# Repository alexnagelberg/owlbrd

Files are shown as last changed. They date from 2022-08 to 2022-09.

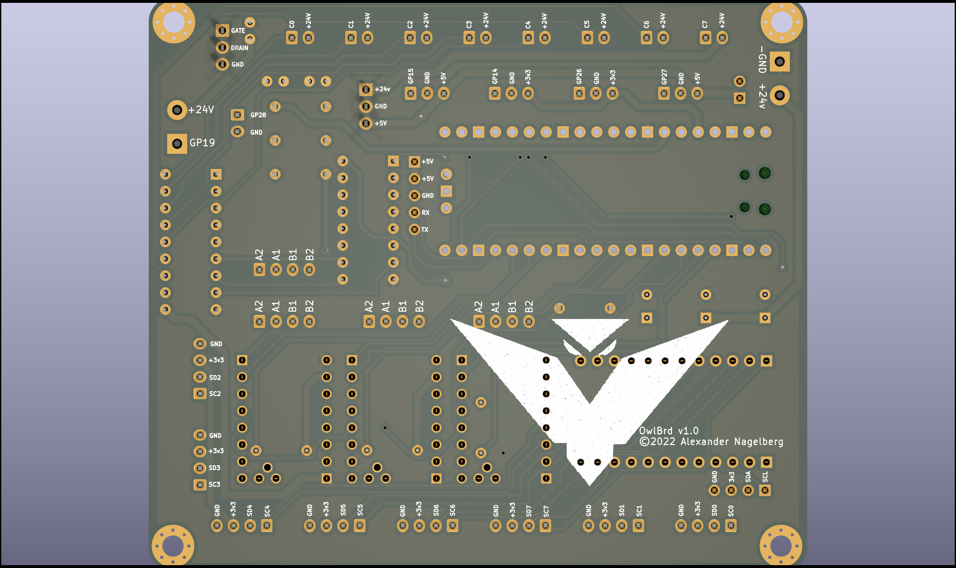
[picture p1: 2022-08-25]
images/back.png

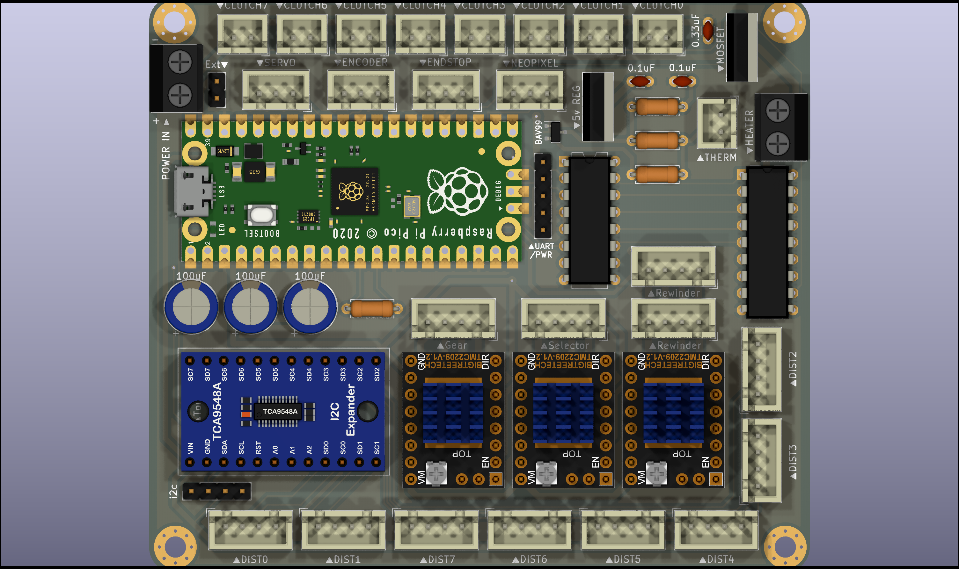
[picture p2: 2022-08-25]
images/board.png

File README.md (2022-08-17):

# OwlBrd
This board was made to supersede EasyBrd but it has a lot more to it so for cost or complexity, you can pick and choose what you want. The only section needed to drive 8 spools is the core section, ideally with distance sensors as well. Most of these parts can be found [in the US] on Amazon/Digikey and should be widely available and low cost and swappable with different manufacturers, the one exception being the optional TCA9548A breakout which only works with Adafruit's (maybe in future I'll add another row of pins to allow the hiletgo variants, but some workarounds can be done).

All the boards can be soldered either directly down or put down a set of headers so the boards can be removed/replaced. I would maybe take care with the TMC drivers as there's a resistor under each, but you could also solder the resistors on the bottom side if there's concerns of heat/proximity without a header -- probably shouldn't be an issue at all.

## BOM (split by functionality)

### Misc (listed again throughout sections)
 - Dupont male/female headers ([Amazon Affiliate](https://amzn.to/3ps0VLI))
 - Resistors - 1k, 10k, 2.37k, 4.7k used throughout (kit: [Amazon affiliate](https://amzn.to/3c7XxCF))
 - Ceramic capacitors: 0.33uF, 0.1uF used in ERCF/heater (kit: [Amazon affiliate](https://amzn.to/3wbLxqx))
 - Electrolytic capacitors: 100uF 25v used in ERCF/rewinder (kit: [Amazon affiliate](https://amzn.to/3Qs2sNM))
 - JST-XH connectors: 2-pin, 3-pin, 4-pin (kit: [Amazon affiliate](https://amzn.to/3AnAbBp))
 - Screw terminals for power/heater ([Amazon affiliate](https://amzn.to/3T8kE0O))

### Core (Rewind Stepper + Clutches)
- Raspberry Pi Pico ([[Digikey](https://www.digikey.com/en/products/detail/raspberry-pi/SC0915/13624793)] headers are optional)
- BTT TMC2209 x1 ([[Amazon affiliate](https://amzn.to/3prqGvD)] headers encouraged, note that UART is currently wired to the 4th pin and some like FYSETC use the 5th pin. You might be able to resolve this with a jumper on the pins on top?)
- 74HC238 DIP ([Amazon affiliate](https://amzn.to/3PAAPkm)) for clutch (addresses 8 pins using 3 GPIO)
- ULN2803A DIP ([Amazon affiliate](https://amzn.to/3QPcatl)) for clutch (drives 8 clutches using one IC)
- Screw terminal for power
- Resistors: 10k (x1), 1k (x1)
- JST-XH 2 pin female (x8) for clutches
- JST-XH 4 pin female (x2) for rewinder steppers
- Electrolytic capacitor: 100uF 25v

### Distance Sensors
- Adafruit TCA9548A ([Amazon affiliate](https://amzn.to/3wdmtQd) or [adafruit](https://www.adafruit.com/product/2717)) breakout (headers optional, cheaper generics available but one side is slightly wider by like 2.5mm -- might be able to rig something to fit it or could use wires)
- JST-XH 4 pin female (x8) for each sensor

### ERCF
- BTT TMC2209 x2 ([[Amazon affiliate](https://amzn.to/3prqGvD)] headers encouraged, note that UART is currently wired to the 4th pin and some like FYSETC use the 5th pin. You might be able to resolve this with a jumper on the pins on top?)
- L7805CV ([Amazon affiliate](https://amzn.to/3zYoTTM)) 5v linear regulator (probably plenty of substitutions for this but should be readily available -- any 5v regulator with same pinout should work) for supplying 5v power on board
- Resistors: 10k (x2)
- Ceramic capacitors: 0.33uF x1, 0.1uF x1
- Electrolytic capacitors: 100uF 25v (x2)
- JST-XH 3 pin female (x4) for servo, encoder, endstop, and optional neopixel/misc
- JST-XH 4 pin female (x2) for selector/gear steppers

### Heater
- IRLB8721PBF ([Amazon affiliate](https://amzn.to/3A3fAC1)) MOSFET (probably lots of substitutable options but should be readily available)
- BAV99 SMD ([[Amazon affiliate](https://amzn.to/3Pub5Gj)] only surface mount component -- shouldn't be too difficult to solder or need anything special, needed for thermistor)
- Screw terminal (or connector of your choice) for heater
- Resistors: 2.37k (x2), 4.7k (x1)
- Ceramic capacitor: 0.1uF
- JST-XH 2 pin female (for thermistor)

### UART
There's a breakout for UART with power for pi. If you use UART, and don't connect pico to USB, you'll want to put a header and jumper on J29 Ext Power so that it powers the pico from the 5v regulator. Install the 0.33uF and 0.1uF capacitors and L7805CV from ERCF section to get 5v power if needed.

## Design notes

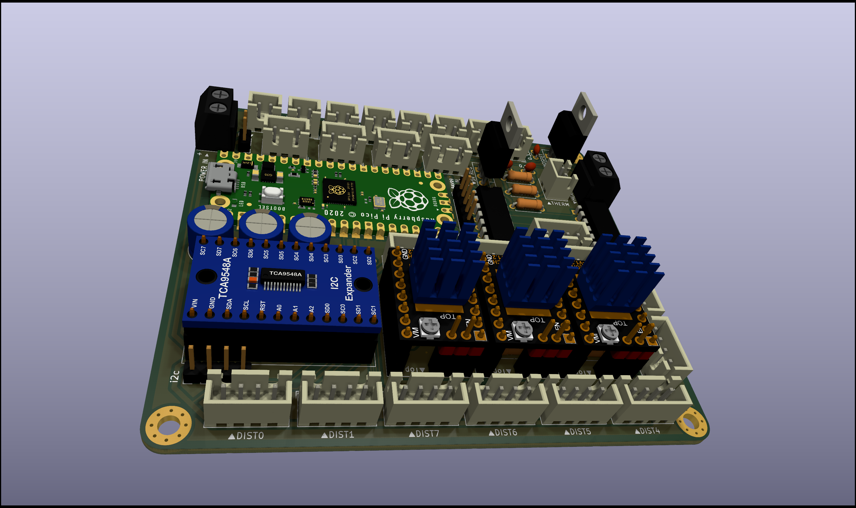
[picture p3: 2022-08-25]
images/board2.png

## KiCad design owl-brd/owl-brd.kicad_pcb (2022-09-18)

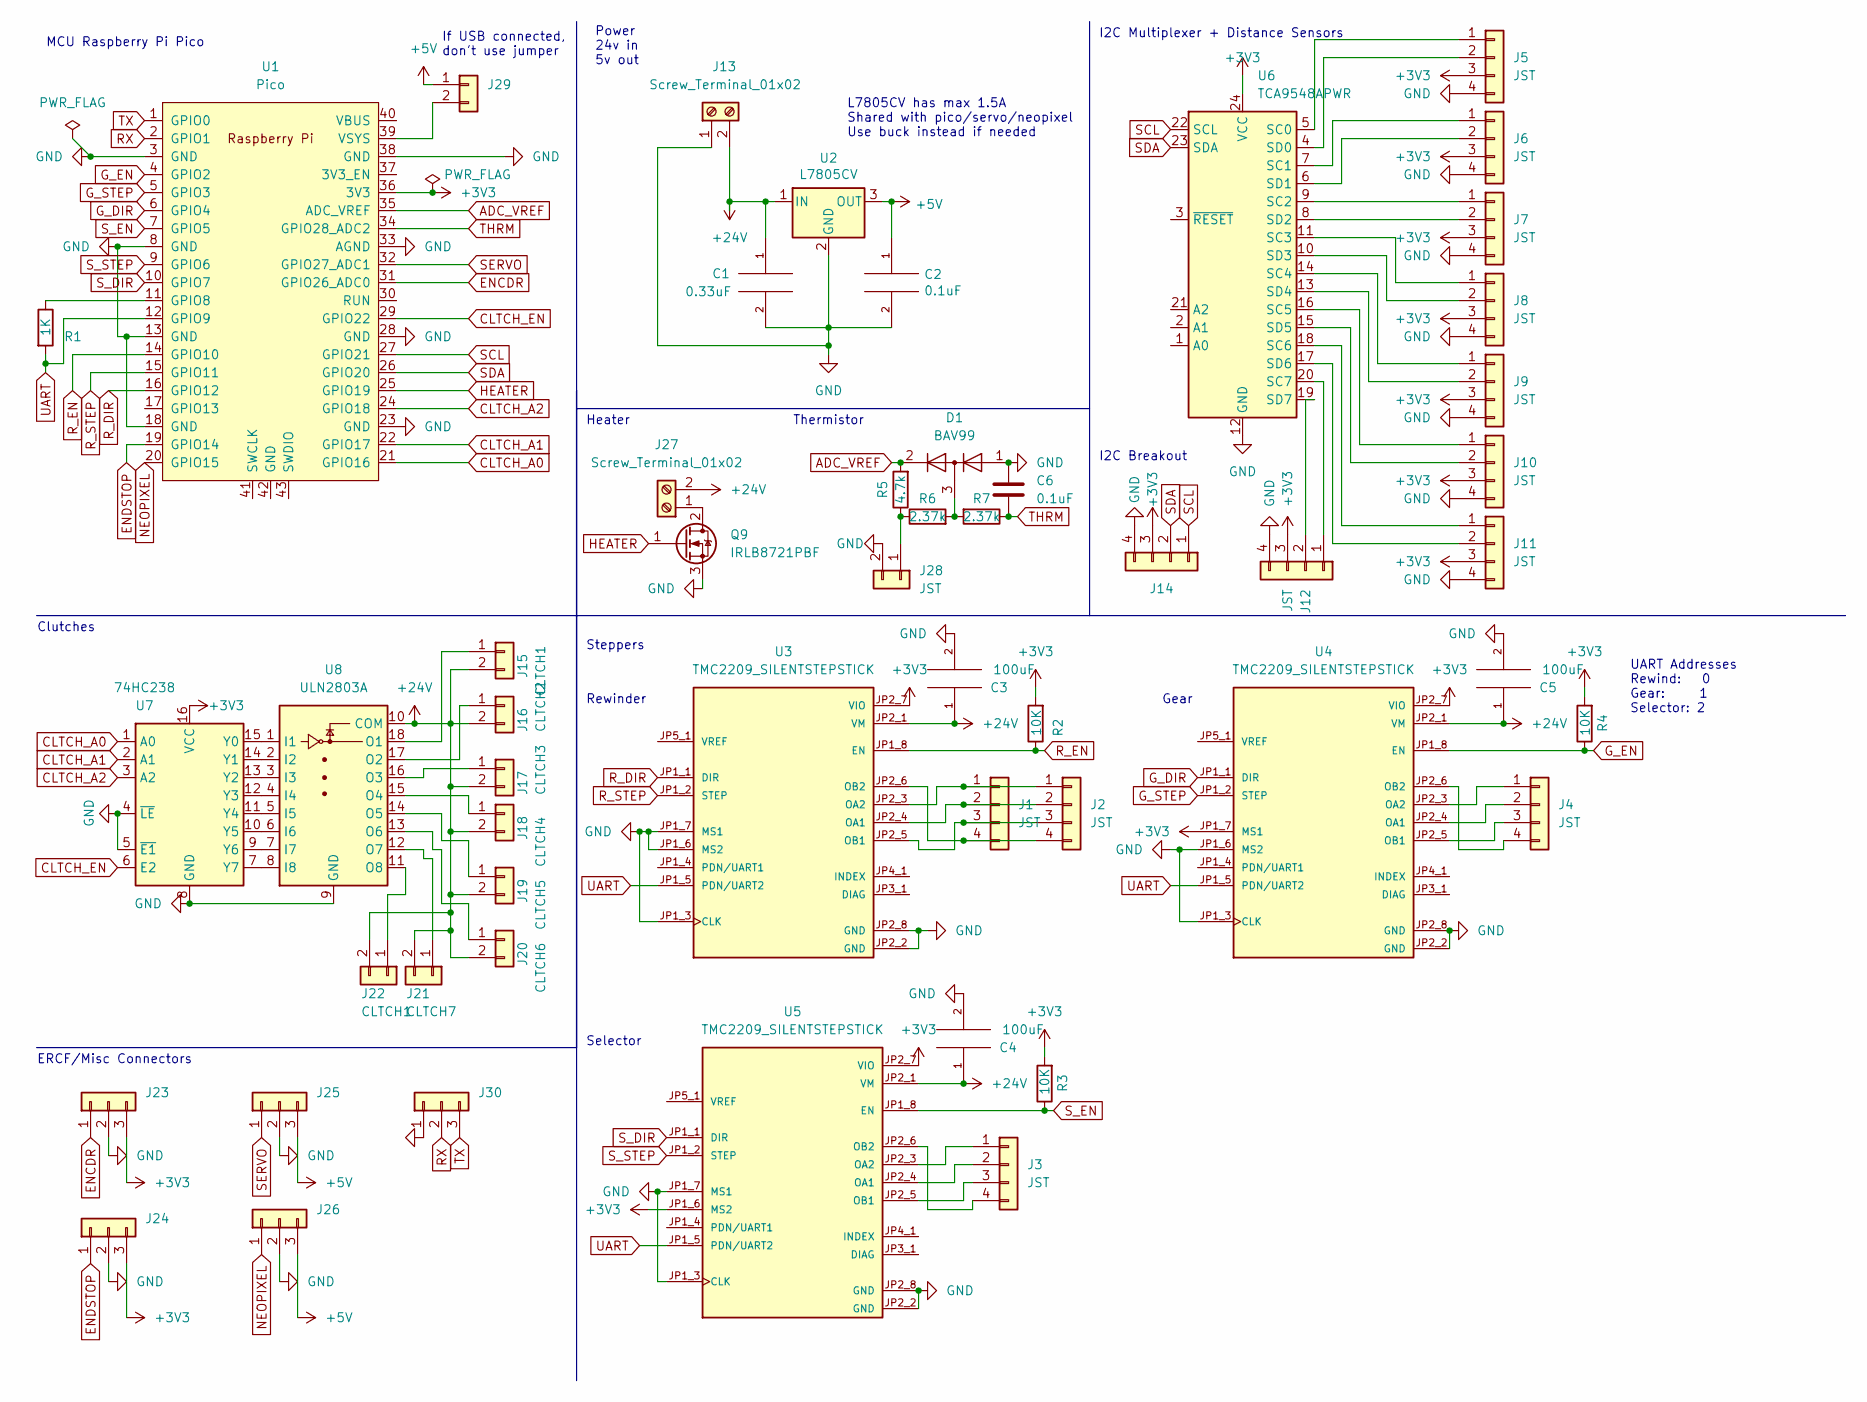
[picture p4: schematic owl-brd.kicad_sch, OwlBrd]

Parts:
C1: 0.33uF; C_Disc_D3.0mm_W1.6mm_P2.50mm
C2, C6: 0.1uF; C_Disc_D3.0mm_W1.6mm_P2.50mm
C3, C4, C5: 100uF; CP_Radial_D8.0mm_P3.50mm
D1: BAV99; SOT-23
J1, J2, J3, J4, J5, J6, J7, J8, J9, J10, J11, J12: JST; JST_XH_B4B-XH-A_1x04_P2.50mm_Vertical
J13, J27: Screw_Terminal_01x02; TerminalBlock_bornier-2_P5.08mm
J14, J29, J30: (no value)
J15, J22: CLTCH1; JST_XH_B2B-XH-A_1x02_P2.50mm_Vertical
J16: CLTCH2; JST_XH_B2B-XH-A_1x02_P2.50mm_Vertical
J17: CLTCH3; JST_XH_B2B-XH-A_1x02_P2.50mm_Vertical
J18: CLTCH4; JST_XH_B2B-XH-A_1x02_P2.50mm_Vertical
J19: CLTCH5; JST_XH_B2B-XH-A_1x02_P2.50mm_Vertical
J20: CLTCH6; JST_XH_B2B-XH-A_1x02_P2.50mm_Vertical
J21: CLTCH7; JST_XH_B2B-XH-A_1x02_P2.50mm_Vertical
J23, J24, J25, J26: JST_XH_B3B-XH-A_1x03_P2.50mm_Vertical
J28: JST; JST_XH_B2B-XH-A_1x02_P2.50mm_Vertical
Q9: IRLB8721PBF; TO-220-3_Vertical
R1: 1K; R_Axial_DIN0207_L6.3mm_D2.5mm_P7.62mm_Horizontal
R2, R3, R4: 10K; R_Axial_DIN0207_L6.3mm_D2.5mm_P7.62mm_Horizontal
R5: 4.7k; R_Axial_DIN0207_L6.3mm_D2.5mm_P7.62mm_Horizontal
R6, R7: 2.37k; R_Axial_DIN0207_L6.3mm_D2.5mm_P7.62mm_Horizontal
U1: Pico; RPi_Pico_SMD_TH
U2: L7805CV; TO-220-3_Vertical
U3, U4, U5: TMC2209_SILENTSTEPSTICK; MODULE_TMC2209_SILENTSTEPSTICK; PARTREV v11
U6: TCA9548APWR; TCA9548A
U7: 74HC238; DIP-16_W7.62mm
U8: ULN2803A; DIP-18_W7.62mm

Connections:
+3V3: J5.3, J6.3, J7.3, J8.3, J9.3, J10.3, J11.3, J12.3, J14.3, J23.3, J24.3, R2.2, R3.2, R4.2, U1.36 (3V3), U3.JP2_7 (VIO), U4.JP1_7 (MS1), U4.JP2_7 (VIO), U5.JP1_6 (MS2), U5.JP2_7 (VIO), U6.24 (VCC), U7.16 (VCC)
+5V: C2.1, J25.3, J26.3, J29.1, U2.3 (OUT)
+24V: C1.1, C3.1, C4.1, C5.1, J13.2, J15.2, J16.2, J17.2, J18.2, J19.2, J20.2, J21.2, J22.2, J27.2, U2.1 (IN), U3.JP2_1 (VM), U4.JP2_1 (VM), U5.JP2_1 (VM), U8.10 (COM)
ADC_VREF: D1.2 (A), R5.2, U1.35 (ADC_VREF)
CLTCH_A0: U1.21 (GPIO16), U7.1 (A0)
CLTCH_A1: U1.22 (GPIO17), U7.2 (A1)
CLTCH_A2: U1.24 (GPIO18), U7.3 (A2)
CLTCH_EN: U1.29 (GPIO22), U7.6 (E2)
ENCDR: J23.1, U1.31 (GPIO26_ADC0)
ENDSTOP: J24.1, U1.19 (GPIO14)
G_DIR: U1.6 (GPIO4), U4.JP1_1 (DIR)
G_EN: R4.1, U1.4 (GPIO2), U4.JP1_8 (EN)
G_STEP: U1.5 (GPIO3), U4.JP1_2 (STEP)
HEATER: Q9.1 (G), U1.25 (GPIO19)
NEOPIXEL: J26.1, U1.20 (GPIO15)
unnamed: D1.3 (K), R6.2, R7.2
unnamed: J1.1, J2.1, U3.JP2_3 (OA2)
unnamed: J1.2, J2.2, U3.JP2_4 (OA1)
unnamed: J1.3, J2.3, U3.JP2_5 (OB1)
unnamed: J1.4, J2.4, U3.JP2_6 (OB2)
unnamed: J3.1, U5.JP2_3 (OA2)
unnamed: J3.2, U5.JP2_4 (OA1)
unnamed: J3.3, U5.JP2_5 (OB1)
unnamed: J3.4, U5.JP2_6 (OB2)
unnamed: J4.1, U4.JP2_3 (OA2)
unnamed: J4.2, U4.JP2_4 (OA1)
unnamed: J4.3, U4.JP2_5 (OB1)
unnamed: J4.4, U4.JP2_6 (OB2)
unnamed: J5.1, U6.5 (SC0)
unnamed: J5.2, U6.4 (SD0)
unnamed: J6.1, U6.7 (SC1)
unnamed: J6.2, U6.6 (SD1)
unnamed: J7.1, U6.9 (SC2)
unnamed: J7.2, U6.8 (SD2)
unnamed: J8.1, U6.11 (SC3)
unnamed: J8.2, U6.10 (SD3)
unnamed: J9.1, U6.14 (SC4)
unnamed: J9.2, U6.13 (SD4)
unnamed: J10.1, U6.16 (SC5)
unnamed: J10.2, U6.15 (SD5)
unnamed: J11.1, U6.18 (SC6)
unnamed: J11.2, U6.17 (SD6)
unnamed: J12.1, U6.20 (SC7)
unnamed: J12.2, U6.19 (SD7)
unnamed: J15.1, U8.18 (O1)
unnamed: J16.1, U8.17 (O2)
unnamed: J17.1, U8.16 (O3)
unnamed: J18.1, U8.15 (O4)
unnamed: J19.1, U8.14 (O5)
unnamed: J20.1, U8.13 (O6)
unnamed: J21.1, U8.12 (O7)
unnamed: J22.1, U8.11 (O8)
unnamed: J27.1, Q9.2 (D)
unnamed: J28.1, R5.1, R6.1
unnamed: J29.2, U1.39 (VSYS)
unnamed: R1.1, U1.11 (GPIO8)
unnamed: U7.7 (Y7), U8.8 (I8)
unnamed: U7.9 (Y6), U8.7 (I7)
unnamed: U7.10 (Y5), U8.6 (I6)
unnamed: U7.11 (Y4), U8.5 (I5)
unnamed: U7.12 (Y3), U8.4 (I4)
unnamed: U7.13 (Y2), U8.3 (I3)
unnamed: U7.14 (Y1), U8.2 (I2)
unnamed: U7.15 (Y0), U8.1 (I1)
RX: J30.2, U1.2 (GPIO1)
R_DIR: U1.16 (GPIO12), U3.JP1_1 (DIR)
R_EN: R2.1, U1.14 (GPIO10), U3.JP1_8 (EN)
R_STEP: U1.15 (GPIO11), U3.JP1_2 (STEP)
SCL: J14.1, U1.27 (GPIO21), U6.22 (SCL)
SDA: J14.2, U1.26 (GPIO20), U6.23 (SDA)
SERVO: J25.1, U1.32 (GPIO27_ADC1)
S_DIR: U1.10 (GPIO7), U5.JP1_1 (DIR)
S_EN: R3.1, U1.7 (GPIO5), U5.JP1_8 (EN)
S_STEP: U1.9 (GPIO6), U5.JP1_2 (STEP)
THRM: C6.2, R7.1, U1.34 (GPIO28_ADC2)
TX: J30.3, U1.1 (GPIO0)
UART: R1.2, U1.12 (GPIO9), U3.JP1_5 (PDN/UART2), U4.JP1_5 (PDN/UART2), U5.JP1_5 (PDN/UART2)

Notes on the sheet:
Rewinder
Thermistor
Selector
Power 24v in 5v out
I2C Breakout
Gear
UART Addresses Rewind: 0 Gear: 1 Selector: 2
Clutches
MCU Raspberry Pi Pico
ERCF/Misc Connectors
If USB connected, don't use jumper
L7805CV has max 1.5A Shared with pico/servo/neopixel Use buck instead if needed
I2C Multiplexer + Distance Sensors
Heater
Steppers

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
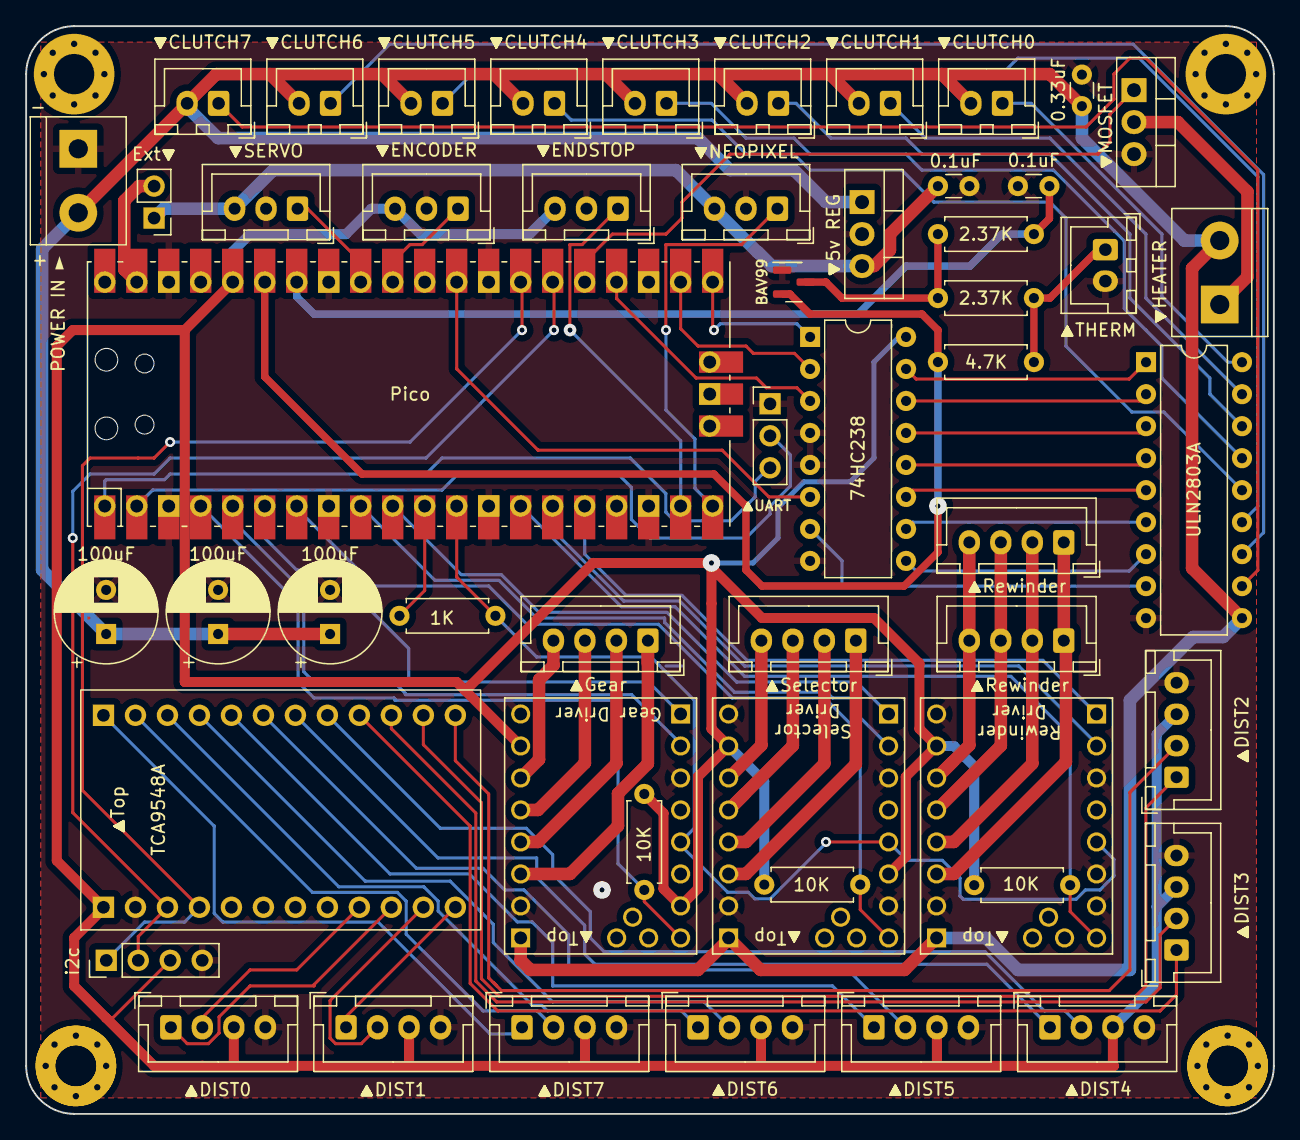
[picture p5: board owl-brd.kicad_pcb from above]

Board: 2 copper layers, 99.1 x 86.4 mm, 53 parts (0 on the bottom side), 78 nets.

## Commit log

2022-08-17 Initial commit -- splitting to own repo
    [owl-brd-B_Cu.gbr, owl-brd-B_Mask.gbr, owl-brd-B_Paste.gbr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]
2022-08-23 - Fix for thermistor mixing vref with 3v3 - Fix footprint for thermistor JST connector - Added enable pin for decoder so that one clutch doesn't have to be on all the time - TODO: rework the CLUTCH p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
    [owl-brd-B_Cu.gbr, owl-brd-B_Mask.gbr, owl-brd-B_Paste.gbr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]
2022-08-25 -3d models/images -Flipped mosfet -Changed UART order (and labels to match pico rx/tx), in line with Pi and SKR headers
    [owl-brd-B_Cu.gbr, owl-brd-B_Mask.gbr, owl-brd-B_Paste.gbr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]
2022-09-02 DIN mounts for owlbrd
2022-09-18 Revision 1.0.1 - Removed 5v on UART pins (output isn't enough for pi) - Notes/minor cleanup for production
    [owl-brd-B_Cu.gbr, owl-brd-B_Mask.gbr, owl-brd-B_Paste.gbr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]

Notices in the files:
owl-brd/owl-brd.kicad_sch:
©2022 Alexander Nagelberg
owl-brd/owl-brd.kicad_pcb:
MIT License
